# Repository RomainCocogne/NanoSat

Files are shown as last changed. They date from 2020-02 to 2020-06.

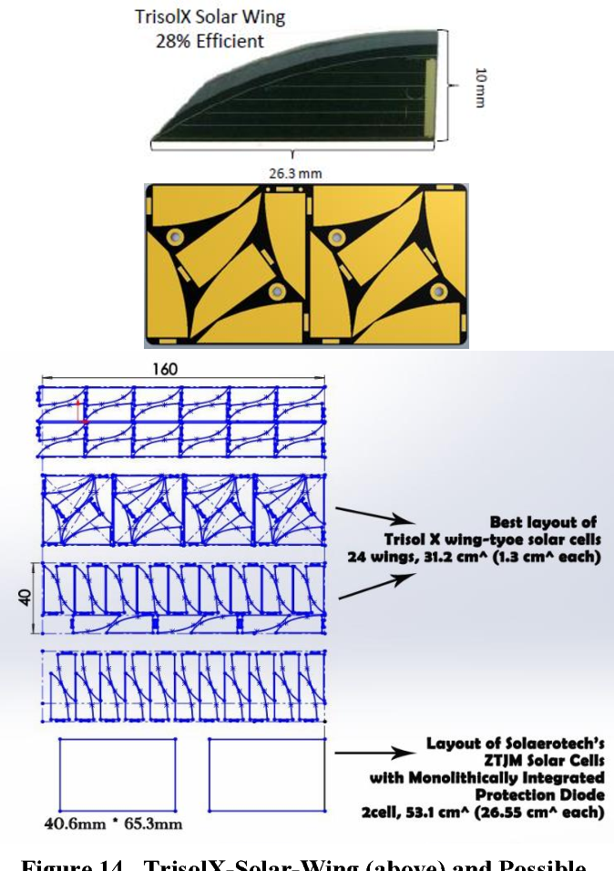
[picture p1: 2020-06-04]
datasheets/TRISOLX/trisolX_layout.png

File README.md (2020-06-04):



### Desciption
This repo is the current work of the Smart Solar Panel Project, an auxiliary project of NiceCube.
NiceCube is a NanoSatellite project.

You can find further informations on this project following this link



### Clone
If you want to clone this repo and continue the project, you need to be aware of some points

  - The code can be used as it is, but you should be carefull if you use another microcontroller. There may be some registers that need to be changed
  
  - The kicad projects use library included into this repo. If you open them as it is you might need to change the access path in kicad parameter tho.

### Contact
You can contact us using the following email adress

camille.brunin@univ-cotedazur.fr

quentin.combal@univ-cotedazur.fr

romain.cocogne@univ-cotedazur.fr

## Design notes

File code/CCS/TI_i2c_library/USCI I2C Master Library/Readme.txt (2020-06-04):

Using the USCI I2C Master

|--DMA Support : All files in this folder can be used ONLY ON MSP430 devices that have the USCI module AND DMA support.
    |------main.c : Application level C file that interfaces with slave MSP430 device. (Use TI_USCI_I2C_slave.c)
    |------TI_USCI_I2C_master_dma.c : Hardware interface level C file that contains all function definitions needed for USCI             initialization and USCI I2C communication.
    |------TI_USCI_I2C_master_dma.h : Header file that contains all definitions used in application/hardware interface files.

|--Without DMA Support : All files in this folder can be used on ANY MSP430 device with the USCI module
    |------main.c : Application level C file that interfaces with slave MSP430 device. (Use TI_USCI_I2C_slave.c)
    |------TI_USCI_I2C_master.c : Hardware interface level C file that contains all function definitions needed for USCI initialization      and USCI I2C communication.
    |------TI_USCI_I2C_master.h : Header file that contains all definitions used in application/hardware interface files.

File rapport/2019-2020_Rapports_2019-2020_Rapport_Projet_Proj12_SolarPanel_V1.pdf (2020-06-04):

1 | Polytech'Nice Sophia, Département électronique Les Templiers 930 Route des Colles - BP 145 06903 Sophia Antipolis Cedex

# Projets Industriels – Elec4

## Année scolaire 2019-2020

# Project Documentation

# Intelligent solar generator for Cubesat

## Version 1.0

Students : Brunin Camille, Combal Quentin,

# Cocogne Romain

# Tutors: Florentin Millour

# Company: Lab Lagrange

Département d partement d’ Electronique lectronique

2 | Polytech'Nice Sophia, Département électronique Les Templiers 930 Route des Colles - BP 145 06903 Sophia Antipolis Cedex

## THANKS

First of all, we would like to thank our project tutor, M. Florentin MILLOUR, for his time, patience and cheerfulness.

Thanks to M. Olivier PREIS too for having brought us to the observatory, it was a really rewarding experience.

Finally, thanks to M. JACOB and M. LANGELLA for their help and educational support.

3 | Polytech'Nice Sophia, Département électronique Les Templiers 930 Route des Colles - BP 145 06903 Sophia Antipolis Cedex

## TABLE OF CONTENT

4 | Polytech'Nice Sophia, Département électronique Les Templiers 930 Route des Colles - BP 145 06903 Sophia Antipolis Cedex

5 | Polytech'Nice Sophia, Département électronique Les Templiers 930 Route des Colles - BP 145 06903 Sophia Antipolis Cedex

# I.Introduction

NiceCube is a nanosatellite project that will allow the Lab Lagrange to do technological demonstrations by performing optical communications between earth and the satellite. NiceCube is a CubeSat type of satellite. It is relatively small, lightweight, and rectangle shaped. The challenges are to make NiceCube self-sufficient in terms of energy, and to gather data from its environment.

A satellite can be powered by different types of generators. The most common and easy-to-use type of generators are solar panels, because they take advantage of the satellite’s long exposure to sunlight in space. They can also be easily integrated in an electronic system. This is what we decide to use to power NiceCube.

Our mission is to conceive a smart solar panel that powers the whole satellite. It will be used as a solar generator and will be able to give us useful real-time information about the satellite. Indeed, we need to measure the current and voltage output of the solar panel, as well as its temperature, the relative location of the sun, and the earth horizon orientation. These measurements are needed to manage the solar cells and to determine the satellite’s orientation. Moreover, the solar cells will need to be electrically protected and individually deactivated if damaged.

In this document we will first go through the requirements of the project, then we will explain how we organized and compare what we planned to do and what we did. Finally, we will go over all the components and prototype’s specifications.

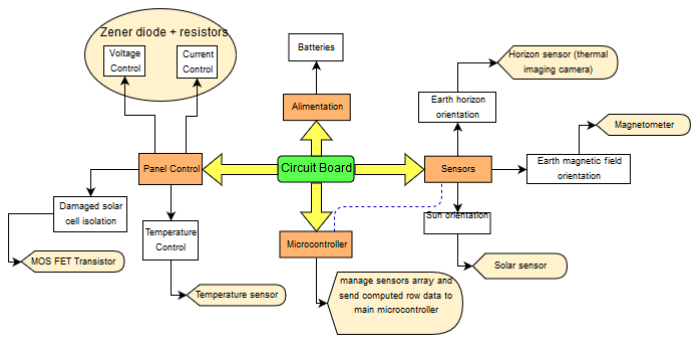
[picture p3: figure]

6 | Polytech'Nice Sophia, Département électronique Les Templiers 930 Route des Colles - BP 145 06903 Sophia Antipolis Cedex

# II.Architecture

## II.1.Block Diagram

Figure II.1 Architecture block diagram

The circuit board will be organized into four different parts described below.

## II.2.The solar panel

The first and core part of our project is the solar panel. The panel control is essential to make sure that the satellite is powered correctly. The panel is a “smart” panel, meaning it can manage itself.

The panel is made of several banks wired in parallel, with each bank made of multiple solar cells wired in series. The voltage output is determined by the number individual cells in each bank, and the current output is set by the number of banks on the panel.

Current and voltage measurements are performed to check if the cells are furnishing the required power for the whole satellite, or to detect a failure in the cell banks. We monitor the temperature of the cells as well with temperature sensors.
If one or several cell banks are damaged, they can be electrically disconnected from the circuit with MOSFET transistors. The command of these transistors is handled by the microcontroller.

## II.3.The main sensors

This is the part of the satellite that is used to gather data from the satellite’s environment. It includes three different types of sensors that are used to determine the current orientation of the satellite.

This part is composed of the following sensors:
- A solar sensor made of two 1-dimensional PSDs (Positional Sensitive Detectors) used to determine the position of the sun relative to the satellite
- A magnetic field sensor used to detect earth’s magnetic field and its relative direction
- A thermal imaging camera used to deduce earth’s horizon orientation from infrared radiation.

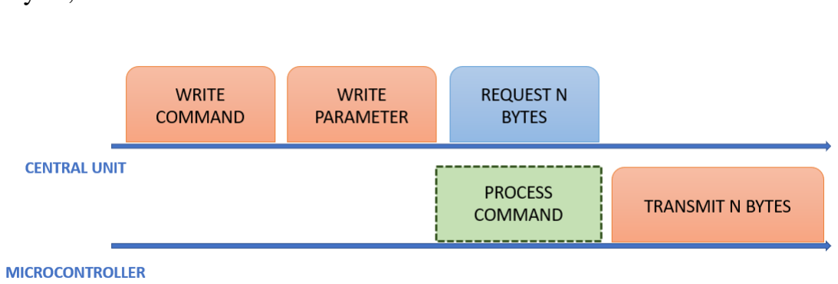
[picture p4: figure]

7 | Polytech'Nice Sophia, Département électronique Les Templiers 930 Route des Colles - BP 145 06903 Sophia Antipolis Cedex

These measurements are computed to deduce three vectors aligned with:
- The orientation of the sun
- Earth’s horizon
- Earth’s magnetic field

These vectors are then used by the satellite’s central unit to regulate its orientation.

## II.4.The microcontroller

The microcontroller’s duty is to manage the solar panel and the sensors. Its main tasks are:
- Managing the solar panel: checking the status of the solar banks through current and voltage measurements. Opening or closing the MOSFET transistors when a cell is damaged.
- Receiving commands from the central unit and sending back the required data
- Managing communication between the sensors

The sensors are accessed using an I²C bus in which the microcontroller acts as the master unit. Likewise, the communication with the central unit uses I²C in which the microcontroller is the slave.

The central unit sends a message containing an 8-bit command and an eventual 8-bit parameter. Upon receiving the command, the microcontroller executes it and holds the response in the buffer. The central unit then asks to receive the processed data, and the microcontroller starts transmitting. Data is transmitted in bytes, LSB first.

Figure II.2 Communication protocol between the microcontroller and the central unit

Below is a list of possible commands:

- READ_SENSOR: asks for a sensor's value. The sensor is specified with a parameter corresponding to a sensor’s id. There is also a specific parameter to ask for a measurement from every sensor.
- LIST_SENSOR: asks for a list of available and functioning sensors
- CONROLLER_STATUS: asks the controller to perform a self-status check and to report any malfunction, such as defective I/Os or unusual temperature.
- CELLS_STATUS: asks the controller to perform a status check on the solar cells.

## II.5.The power supply

This part would be the batteries, charged by our solar panel. However, we are not in charge of the batteries part. We just need to supply enough power to be able to charge them.

Our system needs to be self-sufficient, which mean we must design our system so it can be powered entirely by the solar generator.

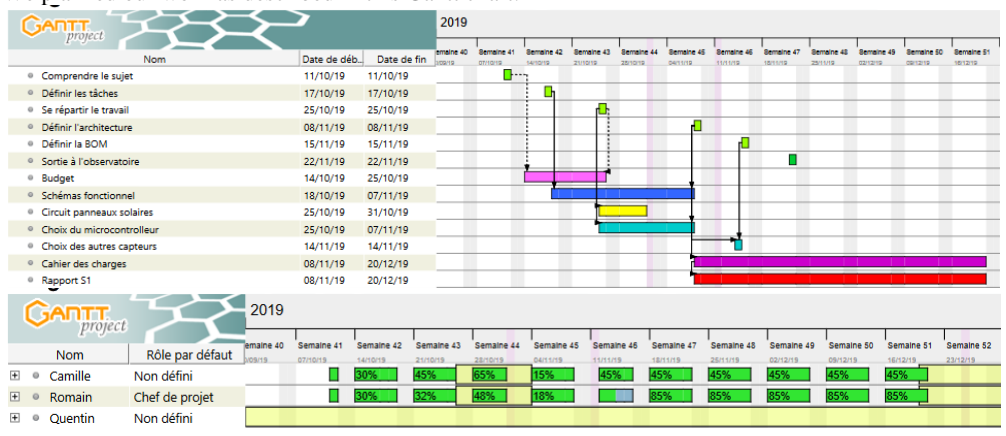
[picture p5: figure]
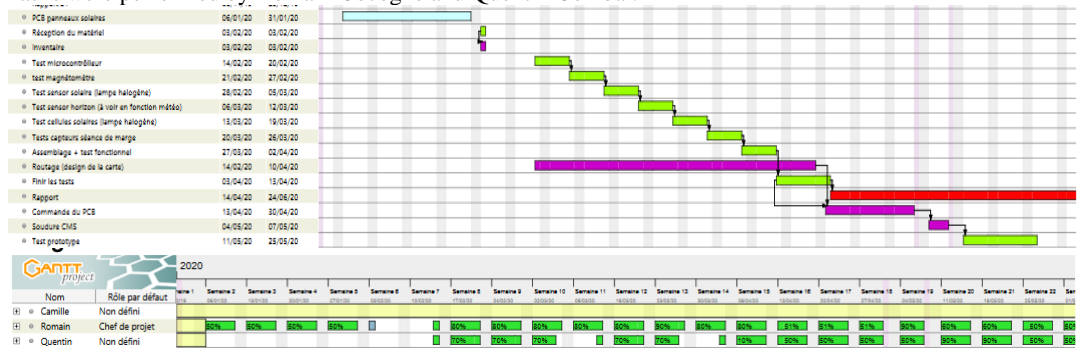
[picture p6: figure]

8 | Polytech'Nice Sophia, Département électronique Les Templiers 930 Route des Colles - BP 145 06903 Sophia Antipolis Cedex

# III.Plan and Tasks

## III.1.Objectives

The first semester was dedicated to defining the specifications of the project, describing a technical solution, and organizing the development. Tasks were performed by Camille Brunin and Romain Cocogne.

We planned our work as described in this Gantt chart.

Figure III.1 Semester 1 planned Gantt chart

During the second semester, we developed and adapted the solutions established during the first semester. Tasks were performed by Romain Cocogne and Quentin Combal.

Figure III.2 Semester 2 planned Gantt chart

## III.2.Reality

For the first semester, we managed to complete all planned tasks on schedule. We did re-shuffle the tasks because we were able to work on tasks in parallel, but overall the planning was accurate. You can see on the resources section that some of them were overloaded, but in reality, the workload was equally supported by both resources. This kind of temporary help can’t be transcribed into the Gantt software.

9 | Polytech'Nice Sophia, Département électronique Les Templiers 930 Route des Colles - BP 145 06903 Sophia Antipolis Cedex

Figure III.3 Semester 1 real Gantt chart

The second semester did not plan out as scheduled. Due to global lockdown caused by COVID-19 pandemic, we re-organized ourselves and changed our objectives, as described in the Adapting to the lockdown section. Overall, Quentin was responsible for most of the software development and Romain was responsible for the hardware development.
We also had one more prototype to do compared to what was planned in semester 1, so we had to squeeze some time for his development. We did have to remove some objectives such as working on the PSD to still be on schedule.

Figure III.4 Semester 2 real Gantt chart

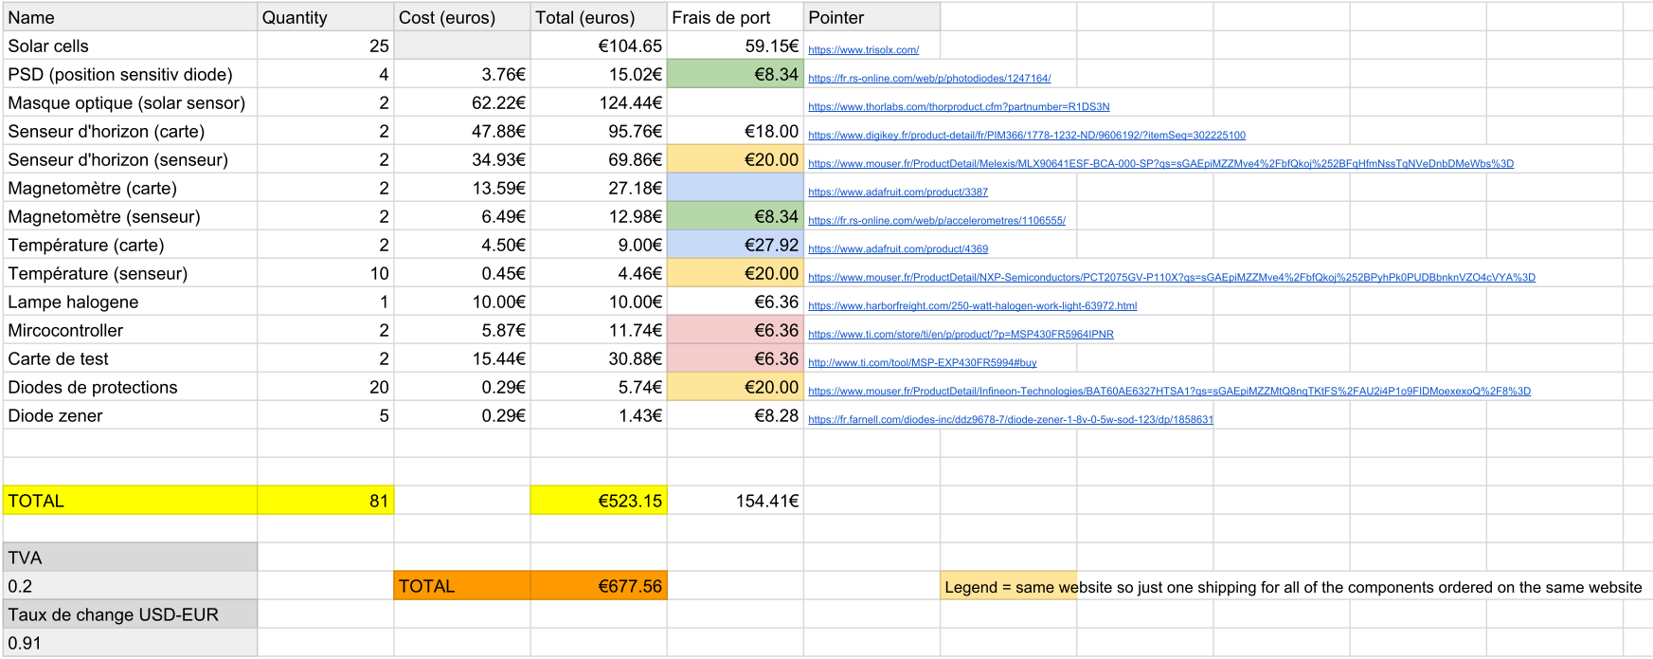
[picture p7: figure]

10 | Polytech'Nice Sophia, Département électronique Les Templiers 930 Route des Colles - BP 145 06903 Sophia Antipolis Cedex

# IV.BOM (Bill of material)

Figure IV.1 First BOM

We can see above the BOM computed from the data we had after one semester of work. After the second semester, all the main components remained the same, but we did add a lot of passives elements. We also added a current sensor, voltage reference and voltage regulator as described in the Development section. You can see below the BOM linked to the second prototype.

Figure IV.2 BOM of second prototype

Item | Qty | Reference(s) | Value | Datasheet
1 | 1 | AC1 | LSM9DS1TR | http://www.st.com/content/ccc/resource/technical/document/datasheet/1e/3f/2a/d6/25/eb/48/46/DM00103319.pdf/files/DM00103319.pdf/jcr:content/translations/en.DM0010331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
2 | 14 | C1, C5, C7, C23, C24, C25, C26, C28, C30, C31, C32, C33, C34, C37 | 100nF | ~
3 | 2 | C2, C3 | 1uF | ~
4 | 6 | C4, C8, C9, C10, C11, C29 | 10uF | ~
5 | 5 | C12, C13, C14, C15, C27 | 10nF | ~
6 | 1 | C22 | 2.2nF | ~
7 | 1 | C35 | 2.2uF | ~
8 | 1 | C36 | 47nF | ~
9 | 3 | D1, D2, D3 | D_Schottky | ~
10 | 1 | IC1 | MLX90641ESF-BAA-000-TU | https://www.mouser.com/datasheet/2/734/MLX90614-Datasheet-Melexis-953298.pdf
11 | 1 | IC2 | PCT2075DP,118 | http://www.nxp.com/docs/en/data-sheet/PCT2075.pdf
12 | 1 | IC3 | MSP430FR5964IPNR | http://www.ti.com/general/docs/suppproductinfo.tsp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
13 | 1 | J5 | HEADER_2x7_2.54MM
14 | 1 | J6 | 532610871 | ~
15 | 14 | Q1, Q2, Q3, Q4, Q5, Q6, Q7, Q8, Q9, Q10, Q11, Q12, Q13, Q14 | RUR040N02HZGTL | ~
16 | 7 | R1, R4, R7, R10, R14, R29, R31 | 20R | ~
17 | 7 | R2, R5, R8, R11, R15, R30, R32 | 1M | ~
18 | 3 | R3, R6, R9 | 100mR
19 | 13 | R12, R13, R16, R17, R18, R27, R28, R39, R40, R41, R42, R43, R44 | 330R
20 | 1 | R19 | 47kR
21 | 11 | R20, R21, R22, R23, R24, R25, R26, R33, R34, R35, R36 | 10k
22 | 1 | R37 | 3.3k
23 | 1 | R38 | 2k
24 | 12 | SC1, SC2, SC3, SC4, SC5, SC6, SC7, SC8, SC9, SC10, SC11, SC12 | Solar_Cell | ~
25 | 1 | SW1 | BP_DROIT_TRAV-switch
26 | 1 | U1 | LT1790ACS6-1.25TRMPBF | LT1790ACS6-1.25#TRMPBF
27 | 2 | U2, U3 | S3274-05
28 | 1 | U4 | NCP59302DSADJR4G | http://ww1.microchip.com/downloads/en/DeviceDoc/MCP14A0303_4_5-Data-Sheet-20006046A.pdf
29 | 1 | U5 | INA3221AIRGVR | Texas Instruments

11 | Polytech'Nice Sophia, Département électronique Les Templiers 930 Route des Colles - BP 145 06903 Sophia Antipolis Cedex

# V.Estimated budget

During the first semester, we were able to estimate the budget by taking into account all of the factors as if we really started this project from scratch. First, we estimated our salaries as engineers and our tutor’s salary. It gave us a total of 6 007€.

Figure V.1 Estimated salaries

Then, we estimated the travel costs for us and our project tutor, which led us to a total of 1 299.96€.

Figure V.2 Estimated travel costs

After that, we had to calculate the costs of the material that we are going to buy and rent, for a total of 2207.56+117 = 2324.56€.

12 | Polytech'Nice Sophia, Département électronique Les Templiers 930 Route des Colles - BP 145 06903 Sophia Antipolis Cedex

Figure V.3 Estimated cost of material

Figure V.4 Estimated cost of renting equipment

Finally, we arrived at a total of:

13 | Polytech'Nice Sophia, Département électronique Les Templiers 930 Route des Colles - BP 145 06903 Sophia Antipolis Cedex

# VI. Components specifications

## VI.1.MICROCONTROLLER

The microcontroller needs to manage the sensor network, control the well-being of the solar cells, and communicate with the satellite’s central unit. It needs to embed at least two hardware I²C modules, so that it can manage one I²C bus for sensor communication, and another bus to exchange data with the central unit. It must have at least 6 analog pins for current and voltage measurements. Most importantly, the microcontroller needs to be optimized for ultra-low power consumption.

Following the advice of our tutor Florentin Millour, we looked towards the MSP430 microcontrollers (https://www.ti.com/lit/ug/slau367p/slau367p.pdf?ts=1590224617008) from Texas Instruments. This family of microcontrollers is known for its low power capabilities and is widely used in similar projects where reducing consumption is essential.
The MSP430FR59XX (https://www.ti.com/lit/ds/symlink/msp430fr5949.pdf?ts=1590224343299) microcomputer family has the following characteristics:
- Up to 256KB of Ferroelectric Random Access Memory (FRAM) with ultra-low power writes
- Optimized Ultra-Low-Power Modes, 350 nA consumption when on standby with a Real Time Clock
- Multifunction I/O ports, 40 to 68 depending on the model
- Up to 4 hardware I2C modules

The MSP430FR59XX (https://www.ti.com/lit/ds/symlink/msp430fr5949.pdf?ts=1590224343299) satisfies all of the aforementioned requirements.

## VI.2.SENSORS

VI.2.1.Solar sensor
We need to sense the satellite’s orientation compared to the sun. Knowing the required angle precision between the satellite and the antenna is 10°, the sensor needs a 3° precision in the worst case. The technology used is a masked one-dimensional PSD (depth of the mask is 1.5mm), so the corresponding length precision of the diode is 78um maximum.
The S3274-05 model gets a 35um maximum precision, which is under the specification. This PSD needs an under 300um wide light ray. The R1DS3N mask has a 10um wide strip line.

VI.2.2.Magnetometer
We need to measure the satellite’s inclination compared to the earth’s surface. We will use a magnetometer to sense the earth’s magnetic field.
As the solar sensor, we need a 3° precision in the worst case.
Knowing the earth’s magnetic field of 05Gauss, we found a maximum error of 26mGauss.
The LSM9DS1’s precision is 0.14mGauss for 4Gauss magnetic fields and under. This corresponds to a 0.02° error. We are well under the specifications.

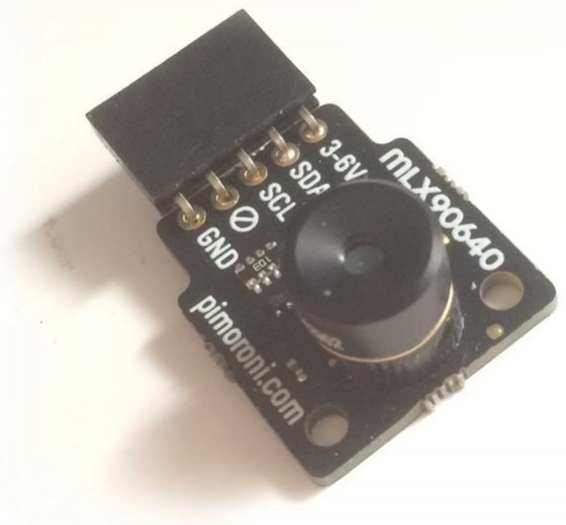
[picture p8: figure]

14 | Polytech'Nice Sophia, Département électronique Les Templiers 930 Route des Colles - BP 145 06903 Sophia Antipolis Cedex

Figure VI.1 LSM9DS1 magnetic sensor on a prototyping board from Adafruit.

VI.2.3.Horizon sensor
We need another vector to angle the satellite compared to the earth, so we need to use a horizon sensor. Just like the other sensor, this one needs a 3° precision in the worst case.
The MLX90641 is a 16x12 pixel thermal camera with a field of view of 110°, giving us a 9°/pixel precision. It means we have a 2.6° precision in the camera. Although we can use this camera, further tests need to be done to see if we are not under the 3° error. If that’s the case, a more power costly camera could be considered. The MLX90640, for example, has a resolution of 32x24 pixels.

Figure VI.2 MLX90640 32x24 thermal camera

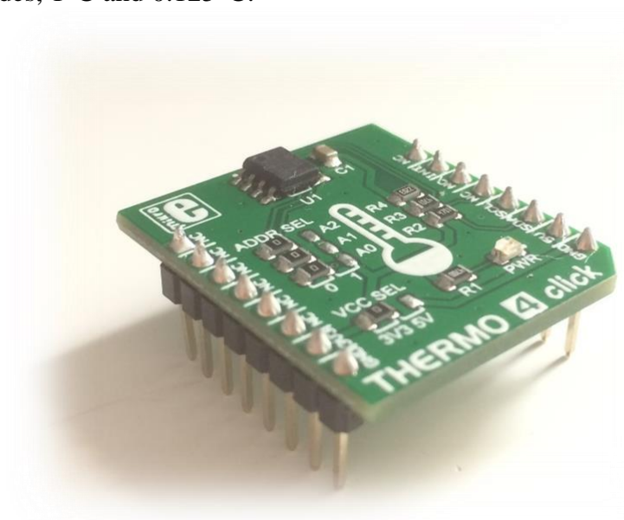
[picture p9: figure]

15 | Polytech'Nice Sophia, Département électronique Les Templiers 930 Route des Colles - BP 145 06903 Sophia Antipolis Cedex

VI.2.4.Temperature sensor
This sensor is needed to control the panel’s temperature. We can put a sensor in the center of the panel and another sensor opposite to the microcontroller to check if there is no overheating. There is no need for a big precision, as we want to measure big temperature variation. A 1°C precision is enough for us. The LM75A has two resolution modes, 1°C and 0.125°C.

Figure VI.3 LM75A temperature sensor on a prototyping board from Mikroe Electronika

VI.2.5.Voltmeter
We need to measure the volt variation (drops and peaks) to check the state of our solar cells. We will use the analog pin of our micro-controller, with a max voltage input of 3.3V. To get maximum precision over the measurement, we take the voltage reference at 1.15V.
To make a voltage reference, we need to use a Zener Diode. As there is no Diode with a Zener voltage under 1.8V, we take 1.8V as a reference. With this, we can detect a voltage drop under 2V, which is enough to detect one solar cell’s failure.

VI.2.6.Amperemeter
To complement the voltage measurement, we need a current variation measurement. We will use resistors in series with the solar cells and measure the resulting voltage. As the solar cells current is around 14mA, the analog pin of our microcontroller will be enough to detect a current drop.

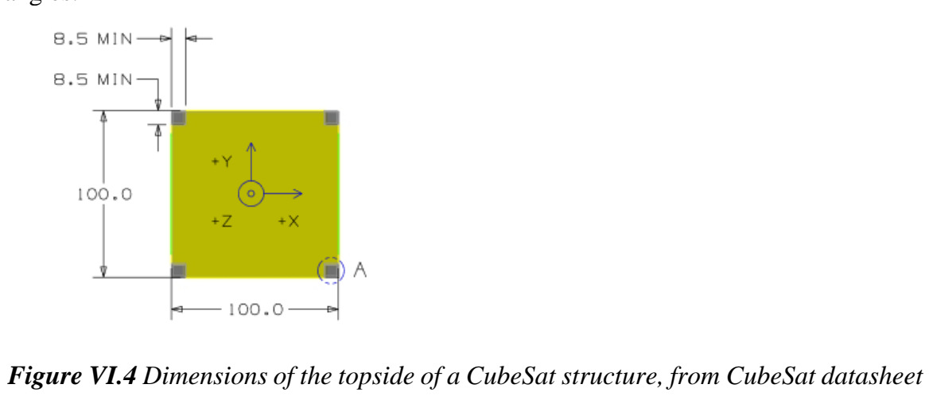
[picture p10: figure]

16 | Polytech'Nice Sophia, Département électronique Les Templiers 930 Route des Colles - BP 145 06903 Sophia Antipolis Cedex

## VI.3.SOLAR CELLS

The system needs to be compatible with the CubeSat structure, meaning a 10x10cm² surface with truncated angles.

The yellow plane above is the available space for our system.
Following the advice of our tutor, we use TrisolX solar cells. TrisolX cells are relatively cheap and are optimized for space applications. They are often used for similar projects.

Each one is approximately 2.6cm². We use a 5mm margin around each cell. Considering the cells will be using 60% of the total panel surface, we can place a total of 12 cells onto our panel.
After testing, the ratio will be adjusted and more panels will be added, but for the prototypes, this ratio will be enough.

The batteries’ control system is GOMSpace, nanopower p31u. (https://gomspace.com/UserFiles/Subsystems/datasheet/gs-ds-nanopower-p31u-27.pdf) As stated in the datasheet, we need to deliver between 4.2V and 8.5V. Knowing the cells are 2.33V max each, we will put 4 cells in series to deliver the correct voltage. As we can use 12 cells, we will make a 4x3 cell matrix.

To protect each line, we put a Schottky diode in series with the 4 cells.
Here is a schematic of one solar bank configuration taken from Prototype 1 schematic.

Figure VI.5 Solar bank schematic

Figure VI.4 Dimensions of the topside of a CubeSat structure, from CubeSat datasheet

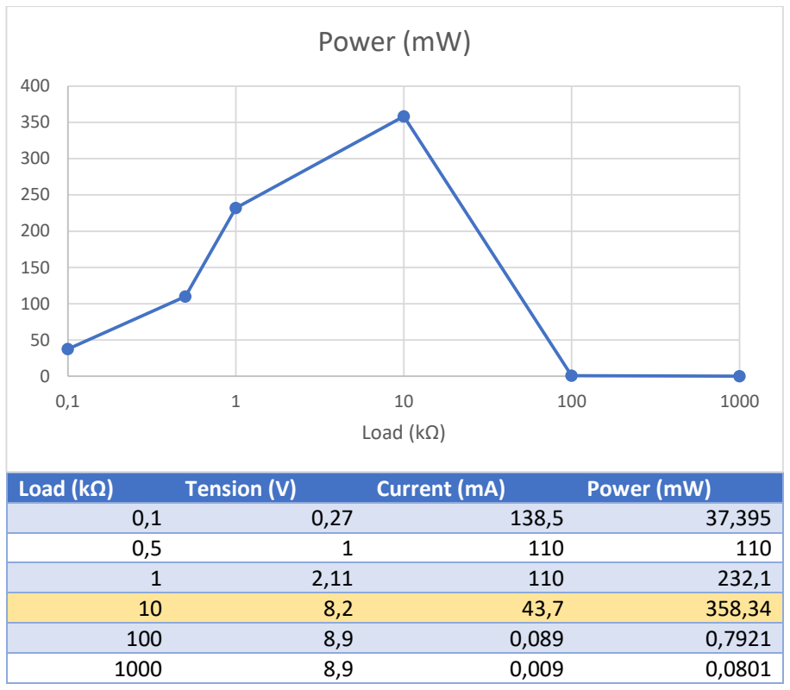
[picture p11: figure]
Load (kΩ); Tension (V); Current (mA); Power (mW)

17 | Polytech'Nice Sophia, Département électronique Les Templiers 930 Route des Colles - BP 145 06903 Sophia Antipolis Cedex

# VII.Development

## VII.1.Solar cells

VII.1.1.Power characteristics
We need to know the best load to put on the solar bank to maximize the power output. To do that, we try different load and measure voltage and current output. In our testing setup, we used a 400W halogen lamp. Halogen lamps provide a luminous spectrum very similar to the sunlight spectrum, and we want to get as close as possible to that spectrum to get realistic tests. The lamp was placed at 10cm from the solar cell testing board. We computed the results into the following curve.

Figure VII.1 Power generation of one solar cell relatively to circuit load.

We can see the optimum load of 10k can provide us with 350mW of power.

VII.1.2.Voltage Reference
At first, we tried to use a Zener diode to provide constant output voltage, but as explained in Prototype 1 category, the result was not satisfactory. We chose to add a dedicated circuit.
We took the MCP1501. It provides a constant 1.25V as reference, with 0.08% of precision. It is possible to shut down the device using the SHDN pin, so we can reduce power consumption.

VII.1.3.Voltage regulator
To power all sensors and the microcontroller, we needed to add a 3.3V voltage regulator. We took the NCP59302DSADJR4G adjustable voltage regulator for his low dropout voltage, its wide output current range and its supply voltage working range (still working with 1.2V input).

18 | Polytech'Nice Sophia, Département électronique Les Templiers 930 Route des Colles - BP 145 06903 Sophia Antipolis Cedex

VII.1.4.Amperemeter
To measure each solar bank’s current input, we first used a shut 20Ω resistor. As explained in Prototype 2, this method doesn’t provide a stable enough output, so we added a dedicated circuit instead.
We chose the INA3221 triple-channel current and voltage monitor because of his I2C compatibility, the ability to monitor 3 solar banks at the same time and his programable alert and warning outputs, allowing us to deport current monitoring to the sensor.
The shut resistors are in turn way smaller, consuming less power from the solar panels.

Figure VII.2. INA3221 TI current and voltage monitor

## VII.2.Microcontroller and sensors interfacing

We were unable to get a micro controller from the MSP430FR59XX family. Instead, we used a MSP430G2553 from Texas Instrument, which provides similar features regarding ultra-low power modes but offers less I/O ports and only one hardware I²C module.

All the sensors we are using communicate their data through I2C busses. The MSP430G2553 has one built-in I2C hardware module that we can use. To develop, calibrate, and prototype our system, we used the MSP430 LaunchPad from Texas Instruments. The LaunchPad is a development board that allows us to easily program our MSP430G2553 microcontroller using a USB connection.

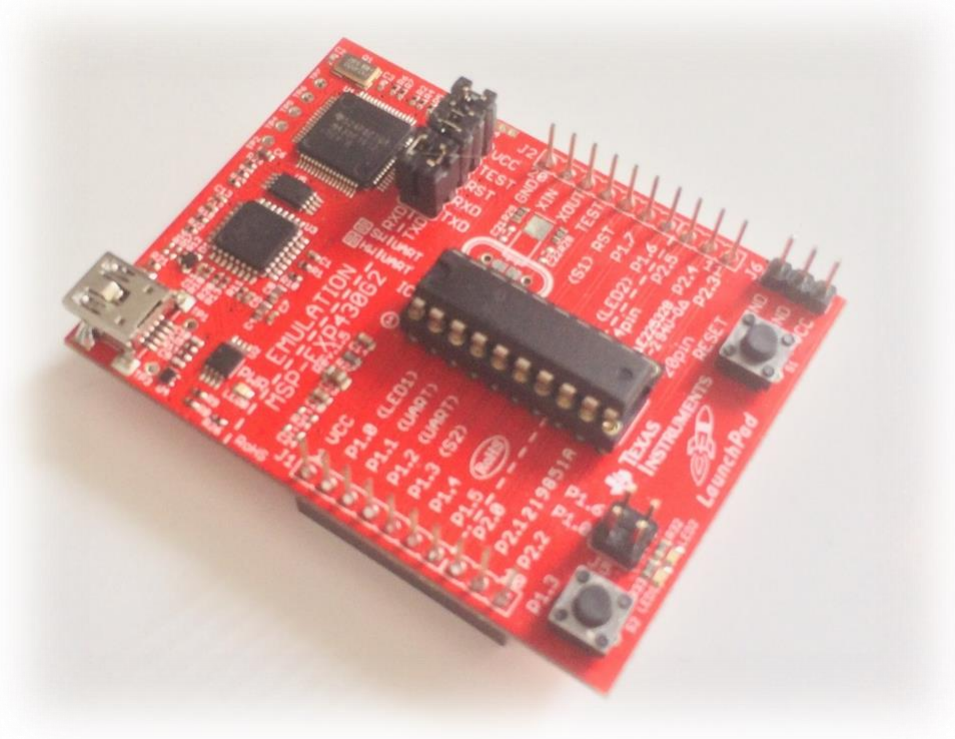
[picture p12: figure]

19 | Polytech'Nice Sophia, Département électronique Les Templiers 930 Route des Colles - BP 145 06903 Sophia Antipolis Cedex

Figure VII.3. MSP430 Launchpad with an MSP430G2553 microcontroller

VII.2.1.Code development
To program the MSP430G2553 and use its hardware modules we used the Energia IDE. Energia is a modified version of the Arduino IDE that comes with custom libraries for specific use with development boards from Texas Instruments, such as our MSP430 Launchpad. This is useful for prototyping because we have access to the standard Arduino libraries that we are used to using. The program is written in a simplified C++ language, identical to the Arduino syntax.
To establish the I2C communication we use the Wire library from the standard Arduino libraries. We developed one code per sensor for independent testing and calibration.
We also need to use the ultra-low power capabilities of the MSP430G2553. This requires a lower level of access than what Energia provides us. We used the Code Composer Studio (CCS) IDE developed by Texas Instruments for their LaunchPad. With CCS we program the microcontroller at Register-Transfer Level using C code. Moreover, this IDE provides useful power optimization advice upon compilation. We can also import code made with Energia into CCS. With this environment, we can first develop a prototype using a higher-level language, and then modify it at a lower level for fine-tuning.

The Wire library was useful for the first functional tests of the sensors, but it is relatively slow, and the library is code heavy. We decided to use the USCI_I2C_master library from TI application examples. It is a light I2C library written in C, we had to tweak it to make it work with our specific model of microcontroller.

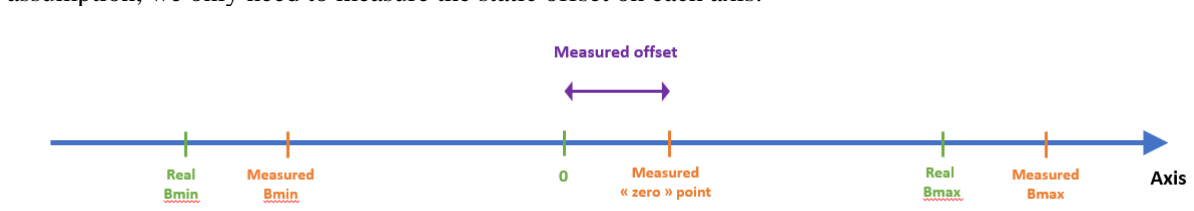
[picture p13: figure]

20 | Polytech'Nice Sophia, Département électronique Les Templiers 930 Route des Colles - BP 145 06903 Sophia Antipolis Cedex

## VII.3.Sensor calibration

Each of our sensor might suffer from a bias, or a distortion, in the measurements. This can happen due to an imprecision during the manufacturing, or a physical phenomenon. This bias is generally small, but we need to take it into account nonetheless, which means we need to be able to measure it. In this section we explain the protocols used to calibrate our sensors.

VII.3.1.LM75A – Temperature sensor
To calibrate the LM75A, we need to measure the temperature of an object whose temperature is known to us. We can then compare the theoretical value to the measured value. The easiest example of such an object is water that is changing phase. We know that the temperature of water stays constant during the transition between two states. We also know the temperatures at which water changes phases. So, if we measure the temperature of water during a phase transition, we should get a consistent result. We decide to measure the temperature of ice cubes that are melting.
We assume the atmospheric pressure during the measurements is equal to 1 bar, which means the temperature of water is 0°C when melting.

Measured temperature of the ice-water mixture: 0.25°C with 0.125°C precision
We determined that our LM75A sensor has a static offset of +0.25°C

VII.3.2.LSM9DS1 – Magnetometer
The magnetometer measures the intensity of the magnetic field along 3 directional axes. We can assume that the axes are aligned as they should be, meaning that they form an orthogonal 3D base. With that assumption, we only need to measure the static offset on each axis.

Figure VII.4 Magnetometer offset schematic

To measure the offset on one axis, a simple test consists of finding the minimum and maximum values on the axis. The offset is the mean value of those extrema. In order to calibrate the LSM9DS1, we need to measure the extrema values on each axis.

The code used to calibrate the sensor can be found in the Annex section. It performs continuous measurements of the magnetic field on each axis and displays the maximum and minimum values on each axis so far. It also displays the resulting offset of those measurements. While this code runs, we rotate the sensor in every direction until the offset readings are stable.

We got the following values:
X offset: +122.5 mGauss
Y offset: +143.36 mGauss
Z offset: +56.35 mGauss

21 | Polytech'Nice Sophia, Département électronique Les Templiers 930 Route des Colles - BP 145 06903 Sophia Antipolis Cedex

VII.3.3.AMG88xx Thermal Camera
Due to time constrain, we only managed to make a working test code with the AMG8833 camera, an 8x8 pixels thermal camera with an Adafruit library. We managed to test the horizon’s detection algorithm with this camera.

Figure VII.3 AMG8833 thermal camera

We need to extrapolate the position of the satellite with the output of the camera, which is an 8x8 pixel array. To get the horizon, we made a linear regression using the matrix formula
(INDEXT
∗ INDEX)

−1

∗ INDEXT
∗ V | (VII.3.3.1)
with V = (

x1
x2
⋮

) , the matrix filled with the pixel position of detected horizon, and INDEX = (

1 1
2 1

⋮ ⋮ ) with

the same length of V.
We get the matrix C = (

a
b

), with a, b the coefficients of the linear expression of the horizon

y = a ∗ x + b | (VII.3.3.2)
We then need to calculate corresponding angles of the satellite position compared to the horizon. We choose the angles α and β as described in the following schematic.

Figure VII.4 Relation between horizon and angles

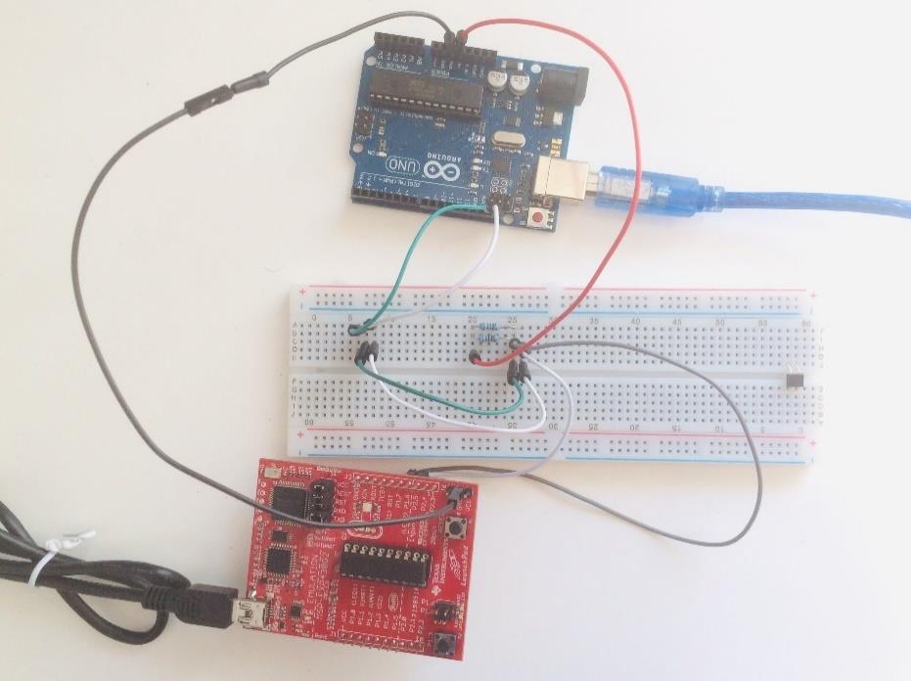
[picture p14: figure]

22 | Polytech'Nice Sophia, Département électronique Les Templiers 930 Route des Colles - BP 145 06903 Sophia Antipolis Cedex

From our linear expression, we can deduce α and β with the following formula in the XY plane (3.5 corresponds to the center of the screen).
αxy = tan⁻¹

(

−1
a
) | (VII.3.3.3)

βxy =

π
6

∗

1
3.5

∗

|3.5(1−a)−b| √a 2+1 | (VII.3.3.4)

And in the YX plane.

αyx =

π
2

− tan⁻¹

(

−1
a
) | (VII.3.3.5)

βyx =

π
6

∗

1
3.5

∗

|3.5(1−a)−b| √a²+1 | (VII.3.3.6)

We did the operation in both planes as, depending of the orientation of the satellite, one projection can be more precise than the other (we have more points in the matrix). We then need to compute the average value.
α =
αyx∗nbpointsyx+αxy∗nbpointsxy nbpointsyx+nbpointsxy | (VII.3.3.7)

β =

βyx∗nbpointsyx+βxy∗nbpointsxy nbpointsyx+nbpointsxy | (VII.3.3.8)

As you can see, we need to guard against limits values, such as a=0. We can explicitly calculate those values when we do the code implementation.
You can see the translation of these equations to an Arduino test code in the Annexes, Code, Thermal Camera section.

## VII.4. Communication with central unit

VII.4.1. Hardware setup
We do not have a lot of specifics about the central unit. But we know that it requires the values read on the sensors and communicates with the microcontroller on an I2C bus. To develop that communication, we used an Arduino Uno R3 board with an ATMEGA328p controller to act as the central unit. We used 10kΩ pull-up resistors on the I2C lines.

Figure VII.5 I2C communication between an MSP430 launchpad and an Arduino Uno R3.

23 | Polytech'Nice Sophia, Département électronique Les Templiers 930 Route des Colles - BP 145 06903 Sophia Antipolis Cedex

Because we are using the MSP430G2553 model instead of the MSP430FR59XX, we only have access to one hardware I2C. Therefore, we can’t test the sensor network and the communication channel with the central unit at the same time, as they require separate I2C buses. We considered using a virtual I2C interface to solve this problem, but we could not find any library for that purpose in C for MSP430 microcontrollers. Moreover, trying to develop our own virtual I2C library would have been time-consuming. We decided to test the communication protocol and the sensor network separately.

VII.4.2.Software setup
The central unit acts as the master on that I2C bus, and the MPS430 microcontroller acts as a slave. The master sends a command to indicate, for example, that it needs a value from the sensors. The microcontroller receives the command, reads one or multiple values from the sensors, processes the values if needed (ex: linear regression to detect the earth horizon as shown in VIII.3.3), and sends the result back to the central unit.

To make the MSP430G2253 act as a slave in the I2C communication we based our program on the TI_USCI_I2C_slave firmware example from Texas Instruments and modified it to make it compatible with our specific model of microcontroller. This small library is written in C and is very light (~100 lines of code). To make the Arduino act as a master we used the Wire library. We wrote a demo program in which the master tests all the available commands.

## VII.5.Prototypes

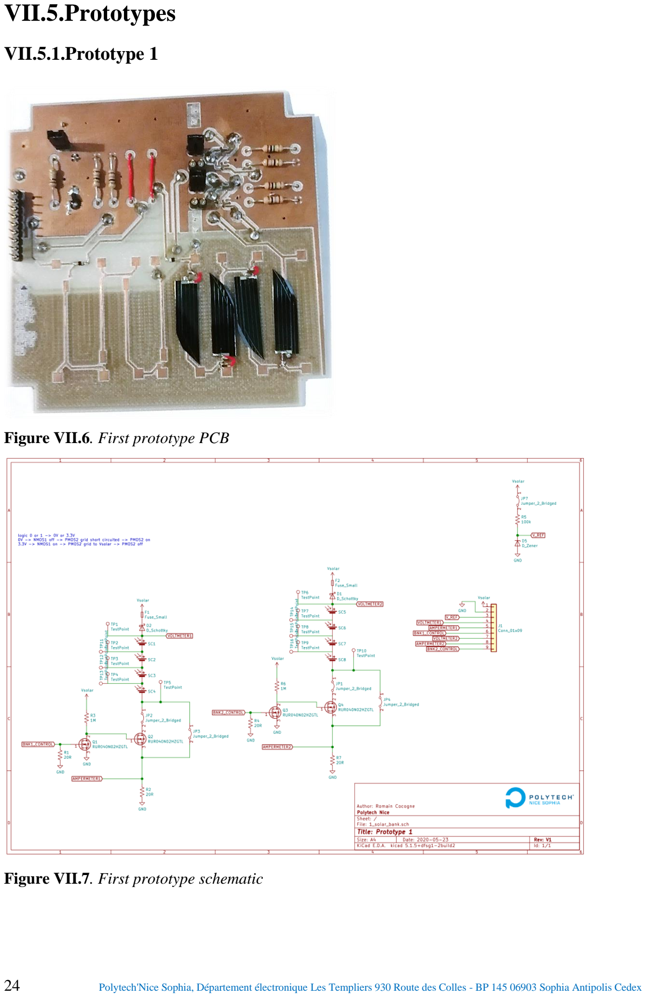
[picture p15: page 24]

24 | Polytech'Nice Sophia, Département électronique Les Templiers 930 Route des Colles - BP 145 06903 Sophia Antipolis Cedex

VII.5.1.Prototype 1

Figure VII.6. First prototype PCB

Figure VII.7. First prototype schematic

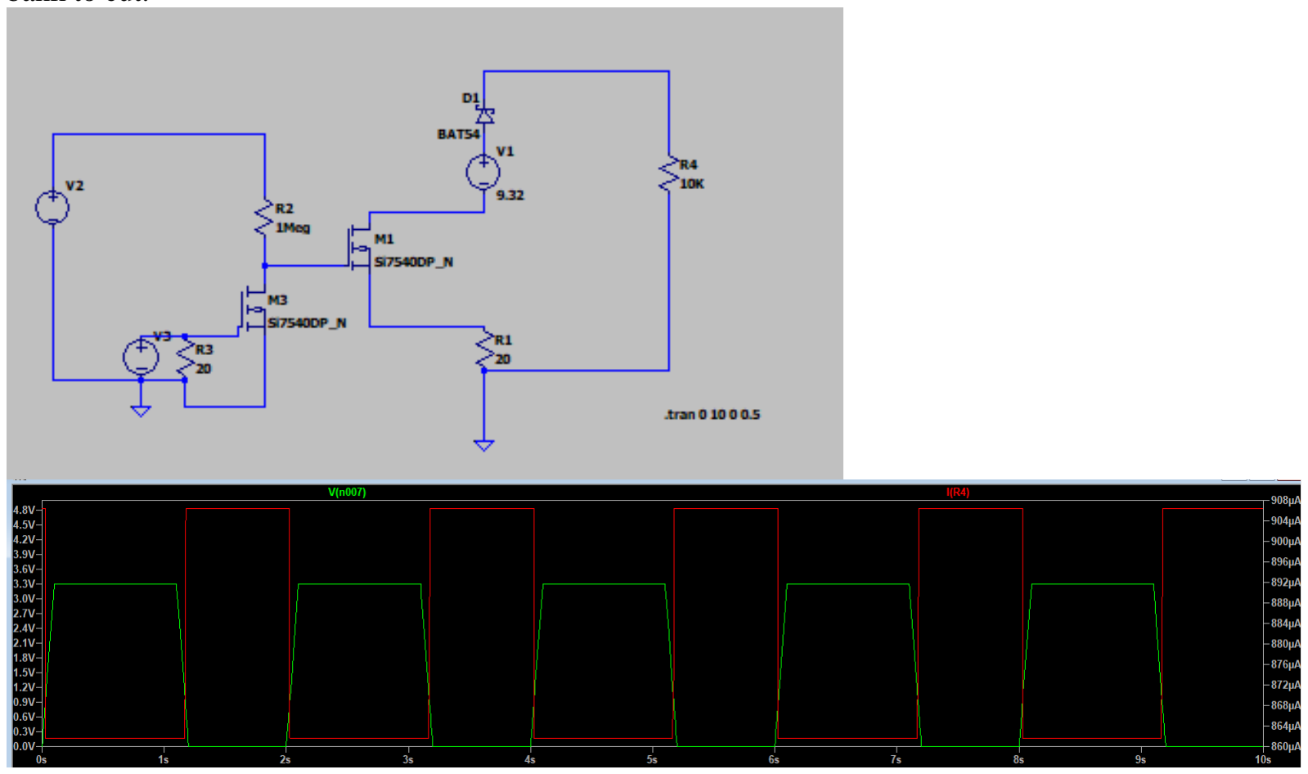
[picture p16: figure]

25 | Polytech'Nice Sophia, Département électronique Les Templiers 930 Route des Colles - BP 145 06903 Sophia Antipolis Cedex

The first prototype aims at testing only some functionalities of the solar panel.
We want to use this prototype to establish f(I) = V of one solar bank, check if the cut-of circuit of the bank works and if Vref is stable enough.
This prototype highlighted that the polarity of our cells was inverted, so the voltage output was negative. The voltage reference was not stable enough with wide variation of input voltage, with around 30% of deviation. We revised the schematic in Prototype 2 to integrate a dedicated reference circuit, explained in the Voltage Reference part.
The footprint of the solar cells was not well adapted and caused some cells to break, so we revised the footprint as seen in the layout of prototype 2.
We tested the amperemeter function and the result was not to our satisfaction. The resistor output was not stable enough to extrapolate running current. We needed a dedicated circuit to measure current with precision. We revised the schematic in Prototype 2 to integrate a dedicated amperemeter circuit, explained in the Amperemeter part.

This prototype was useful to compute the power characteristics curve and find the optimum load to put on the solar panels.
We didn’t manage to test the cut-of circuit because of delays in components delivery. Before printing the second prototype PCB, it is advised to test this feature. We nonetheless did a Spice simulation and the result was to our satisfaction. You can see below the result with V3 in input (green trace) and IR4 in output (red trace). The circuit lets the current flow through the load if the input is a logic ‘0’ and cut the current if the input is a logic ‘1’. This configuration allows the microcontroller to boot up before choosing which solar bank to cut.

Figure VII.8. Simulation of cut-of circuit

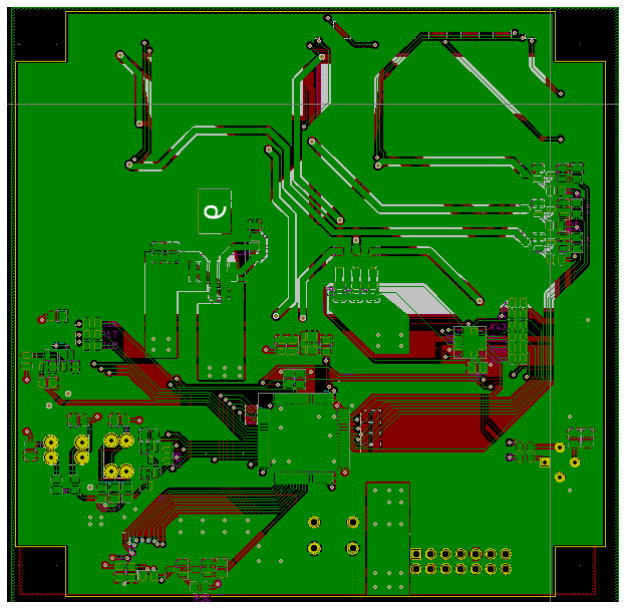
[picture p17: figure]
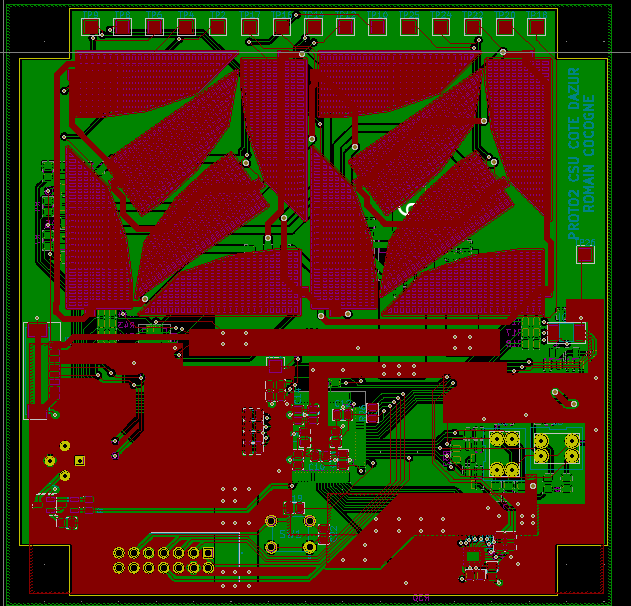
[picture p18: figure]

26 | Polytech'Nice Sophia, Département électronique Les Templiers 930 Route des Colles - BP 145 06903 Sophia Antipolis Cedex

VII.5.2.Prototype 2
For this prototype, we implemented all changes pointed out in prototype 1. You can study the schematics following this link to the Annexes, Schematics part.
We wanted to test the I2C bus and the working of our sensors. This prototype can also be used to test the code integration and the main software.
Due to time constrains, we didn’t print the PCB, but we finished the layout. All the passives components are in 0805 dimensions to ease the soldering further prototypes can use smaller packages to gain space. We have a 2 layers board to reduce production cost, but in fine it should be best to go with a 6 layers board with internal layers as ground or power plane. This will keep all sensitive components protected from space hazards.
We added one more solar bank to test the cube layout you can see below. This should be an optimized layout according to FigureVII.11.

Figure VII.11. Second prototype layout

Figure VII.9. TrisolX layout comparison

27 | Polytech'Nice Sophia, Département électronique Les Templiers 930 Route des Colles - BP 145 06903 Sophia Antipolis Cedex

The prototype is delivering the solar bank voltage as well as the I2C bus pins. This bus can’t be used to test I2C communication with the CubeSat’s main microcontroller. Its only use is to monitor the communication between our microcontroller and the sensors array.
The microcontroller is programmable through a JTAG connection.
To measure all the different voltages on this board, you can use the tests pads marked on the front face.

Here are some improvements and new features to add in the next prototype.
- Implement an EEPROM next to the microcontroller to keep permanent logs of sensors and panels state
- Add LED indicators to check if the board is powered up
- Add access pin to the microcontroller
- Add a second I2C bus output to try communicating with the main microcontroller

28 | Polytech'Nice Sophia, Département électronique Les Templiers 930 Route des Colles - BP 145 06903 Sophia Antipolis Cedex

# VIII.Challenges

## VIII.1. Technological challenges

One of the challenges that we faced was that we needed to learn how to use the MSP430 microcontroller and its embedded hardware modules. Setting up an efficient programming environment for prototyping took longer than we expected. The Launchpad development board does not benefit from a large community support, unlike Arduino boards for example. We could not always find existing libraries to answer our needs, which led us to rewrite libraries using register transfer operations. This made the development take more time than what we originally expected.

The routing of the second prototype was also a big challenge. Indeed, the board is inside a 100cm² square and a lot of components needs to fit in there. The 2 layers constrain did add a lot of complexity because some tracks were intertwining and crossing each other most of the time. Changing the orientation and disposition of the sensors helped resolve most of the problems, but sometimes we had no other choice but to modify the microcontroller pinout.

## VIII.2. Adapting to the lockdown

The global lockdown that started on March 16th in France in reaction to the COVID-19 pandemic was a major slowdown in the development of our project, due to its hardware nature. We had to reconsider our objectives and our organization.

We split the components so that we could work on separate parts and continue the development. Romain kept the solar cells, the halogen lamp, the first prototype, and soldering materials to be able to perform more tests and develop the schematic and routing for the second prototype. Quentin kept the microcontroller development board, the thermometer, and the magnetic sensor to develop the sensor interfacing and the I2C communication. Regarding the thermal cameras, we both kept one model, the 8x8 AMG88 for Romain and the 32x24 MLX90640 for Quentin. We also both kept one photo diode to try to develop the solar sensor. Fortunately, we had some electronic components at our homes, as well as Arduino boards that were very useful for prototyping.

To keep in touch with our tutor Florentin Millour, we organized weekly group calls using Skype and Zoom. It was essential to keep Mr. Millour informed on the advancements of the project, and to get his advice on where to put our focus in the development.

We tried to issue a new RS order, but due to unforeseen delays caused by current circumstances, we were not able to receive the components in time. Our tutor did provide us with some of his personal hardware such as his own MSP430 development board but there was some mismatch between the microcontrollers model and some features were not tested.

We ultimately had to lower our objectives. As we did not have access to the electronic lab anymore, we were unable to produce our second prototype. Instead we decided to focus on making the core parts of the project functional.

29 | Polytech'Nice Sophia, Département électronique Les Templiers 930 Route des Colles - BP 145 06903 Sophia Antipolis Cedex

# IX.Current state of the project

The core parts of our project, like the schematic for the solar cells or the I2C communication, are working as intended. The next step in the project would be to produce a prototype that links those core parts to test their interactions. We could not achieve all the objectives that we had planned. However, we provided a baseline of the different parts so that the project can be continued in the future.

In the following sections we summarize which parts of the project we consider functional, and which parts require further work.

## IX.1.Parts that are functional

IX.1.1.Solar cells electronic schematic
We designed an electronic schematic to manage the solar cells. The solar panel groups the solar cells into banks that deliver an 8.2V output with a max current of 43,7mA per bank. Individual banks can be disconnected by toggling an input on MOSFET transistors.
Simulations of this electronic system were performed on LTSpice and were successful. However, we could not perform practical tests as we could not access the equipment to produce a prototype. Further testing would be needed to ensure that the system works as intended with the microcontroller ports.

IX.1.2.Thermometer, magnetic sensor
We wrote functional programs in C for both the thermometer and the magnetic sensor. The program files are light and use direct register access on the hardware I2C module, making the execution relatively fast. As of now, each sensor has its own program in separate CCS project directories, but the two programs can be easily combined assuming the sensors are on the same I2C bus. The library used to exploit the I2C module can be used as a baseline to write programs for the other sensors.

IX.1.3. 8x8 thermal camera
We performed tests on the AMG8833 8x8 thermal camera and implemented the algorithm described in Sensor calibration Section. Those first tests were successful in detecting the horizon. However, this sensor was only tested on an Arduino Uno R3 board, using a specific library from Adafruit written in C++. Tests on the MSP430 Launchpad could not be performed due to the lockdown.

Moreover, further tests need to be done to measure the precision of the resulting values α and β and determine if the resolution provided by an 8x8 grid is enough.

IX.1.4. Communication with the central unit
The communication protocol between the microcontroller and the central unit is functional. As of now, four commands are implemented, with one command accepting one parameter. More specifications on the central unit could require adding more commands to the command set. This can be done easily as the code structure that handles commands on the microcontroller is flexible. However, the code should be tested with a network of sensors using a MSP430FR59XX microcontroller that has multiple hardware I2C modules.

30 | Polytech'Nice Sophia, Département électronique Les Templiers 930 Route des Colles - BP 145 06903 Sophia Antipolis Cedex

IX.1.5. PCB
We managed to complete one working prototype validating the following requirements:
- The power output
- The circuit protection of solar cells
The other hardware requirements were not tested but the groundwork is already done. The PCB layout of a nearly full featured board is ready to be printed and tested. The layout was checked by the website JLCPCB (https://jlcpcb.com/) and deemed as sound.

## IX.2. Parts that require further work

IX.2.1. Using the ultra-low power features of the microcontroller
We were not able to measure the consumption of the microcontroller when it is in function. We also did not exploit the low-power modes in our prototypes, as we wanted to make the design functional before trying to reduce power consumption. However, the environment we used to develop our code, Code Composer Studio, has an “Optimization advice” feature that helps reduce power consumption and optimize computation time. Once we have a working prototype, we can quickly optimize power consumption using this feature

IX.2.2. 32x24 Thermal camera
As mentioned above, the 8x8 camera is functional but might not meet our requirements regarding precision. We attempted to use the 32x24 MLX90640 camera and tried prototyping using an Arduino library from Adafruit. However, the program for that camera could not be tested due to memory limitations. The temporary storage that we need for the linear regression algorithm is taking too much space. To use this camera, we would need to write the sensor interfacing program in C and tweak the algorithm so that it uses less temporary storage.

IX.2.3. Solar sensors
We could not design a program to test the solar sensors due to a lack of time. This part needs to be developed as it is an essential sensor to determine the orientation of the satellite.

IX.2.4.Network of sensors
We need to write a program that can read data from multiple sensors on the same I2C bus. We would only need to combine the programs that read one sensor, and make sure each address is assigned to only one sensor. Furthermore, we need to test the sensor network when the microcontroller also communicates with the central unit. We want to make sure that reading and processing the sensor values is fast enough to provide real-time reading to the central unit.

31 | Polytech'Nice Sophia, Département électronique Les Templiers 930 Route des Colles - BP 145 06903 Sophia Antipolis Cedex

# X.References

You can find all datasheets and source documents, as well as original Kicad design and Arduino code on the Github of this project.
https://github.com/RomainCocogne/NanoSat.git

Other links:

Texas Instrument, “MSP430FR599x, MSP430FR596x Mixed-Signal Microcontrollers datasheet”, [SLASE54C]

https://www.ti.com/lit/ds/symlink/msp430fr5949.pdf?ts=1590224343299

Texas Instruments, “MSP430FR58xx, MSP430FR59xx, and MSP430FR6xx Family User Guide”, [SLAU367P]
https://www.ti.com/lit/ug/slau367p/slau367p.pdf?ts=1590224617008

Texas Instruments; “Using the USCI I2C Master” [SLAA382A]

http://www.ti.com/lit/an/slaa382a/slaa382a.pdf

Texas Instruments; “Using the USCI I2C Slave” [SLAA383]

https://datasheet.datasheetarchive.com/originals/library/Datasheet-080/DASF004576.pdf

CubeSat design specification

https://static1.squarespace.com/static/5418c831e4b0fa4ecac1bacd/t/56e9b62337013b6c063a655a/1458157095454/cds_rev13_final2.pdf (https://static1.squarespace.com/static/5418c831e4b0fa4ecac1bacd/t/56e9b62337013b6c063a655a/1458157095454/cds_rev13_final2.pdf)

TrisolX layout

https://d3i71xaburhd42.cloudfront.net/6ffac9621ad9e26aa4264a1be23f66f674bda921/10-Figure14-1.png

GOMspace nanopower p31u, Power supply

https://gomspace.com/UserFiles/Subsystems/datasheet/gs-ds-nanopower-p31u-27.pdf

32 | Polytech'Nice Sophia, Département électronique Les Templiers 930 Route des Colles - BP 145 06903 Sophia Antipolis Cedex

# XI.Annexes

## XI.1.Code

XI.1.1.Thermal Camera

Figure XI.1. Main test code AMG8833, part 1

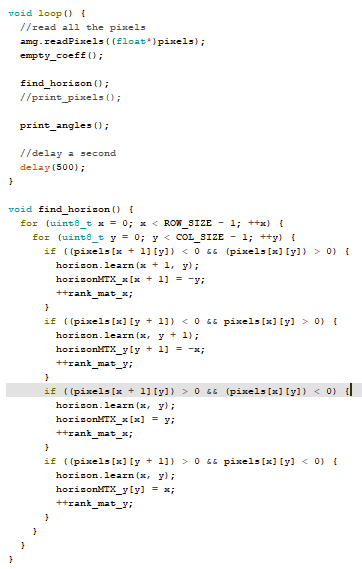
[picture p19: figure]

33 | Polytech'Nice Sophia, Département électronique Les Templiers 930 Route des Colles - BP 145 06903 Sophia Antipolis Cedex

Figure XI.2. Main test code AMG8833, part 2

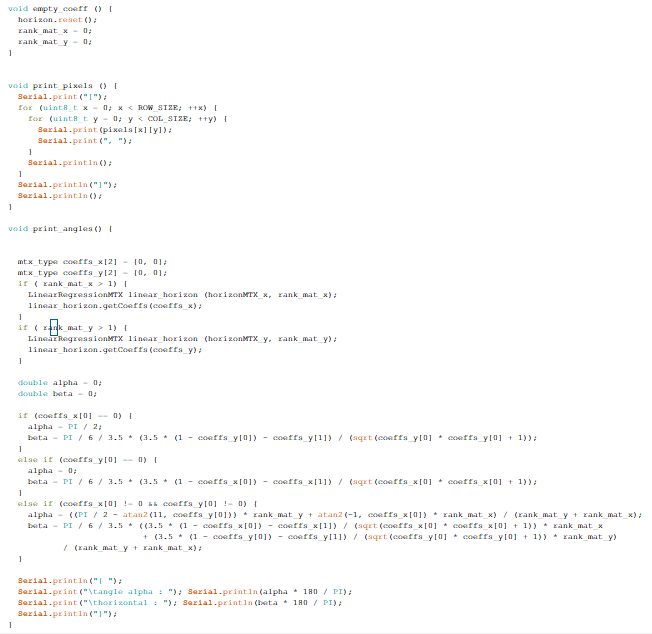
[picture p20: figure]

34 | Polytech'Nice Sophia, Département électronique Les Templiers 930 Route des Colles - BP 145 06903 Sophia Antipolis Cedex

Figure XI.3. Main test code AMG8833, part 3

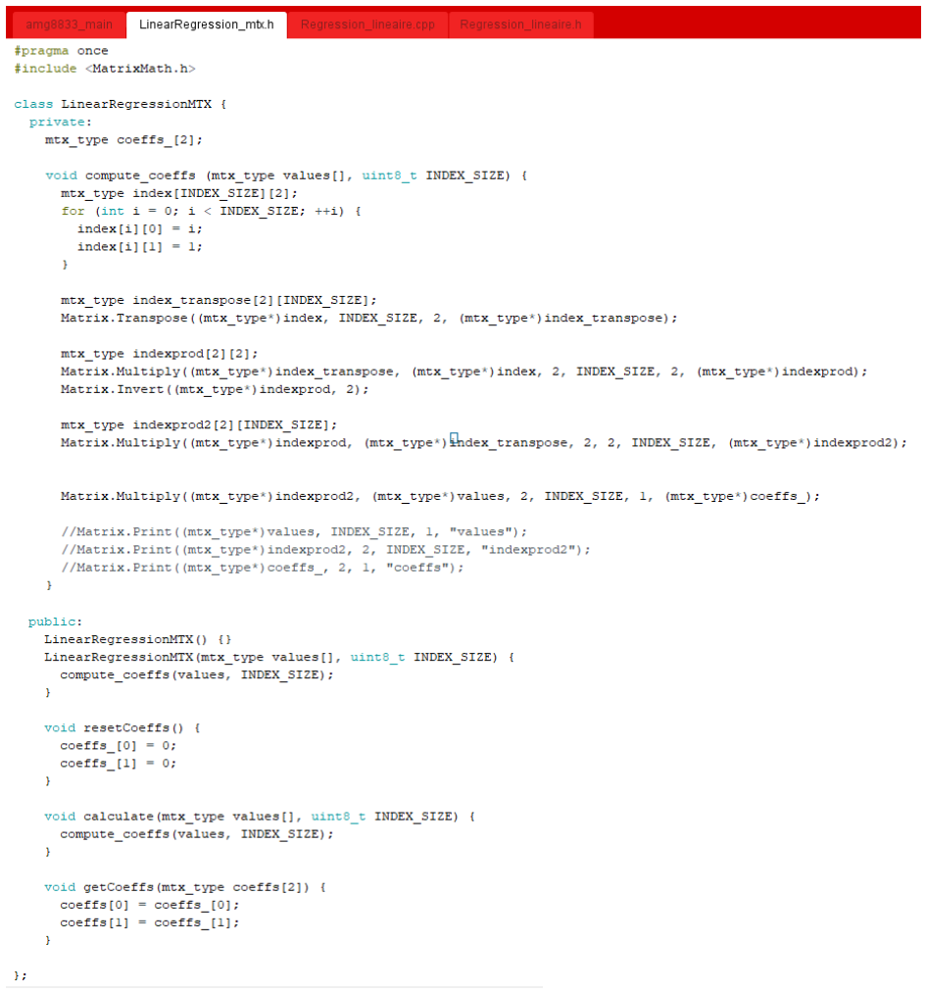
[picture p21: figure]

35 | Polytech'Nice Sophia, Département électronique Les Templiers 930 Route des Colles - BP 145 06903 Sophia Antipolis Cedex

Figure XI.4. Linear Regression class test code AMG8833

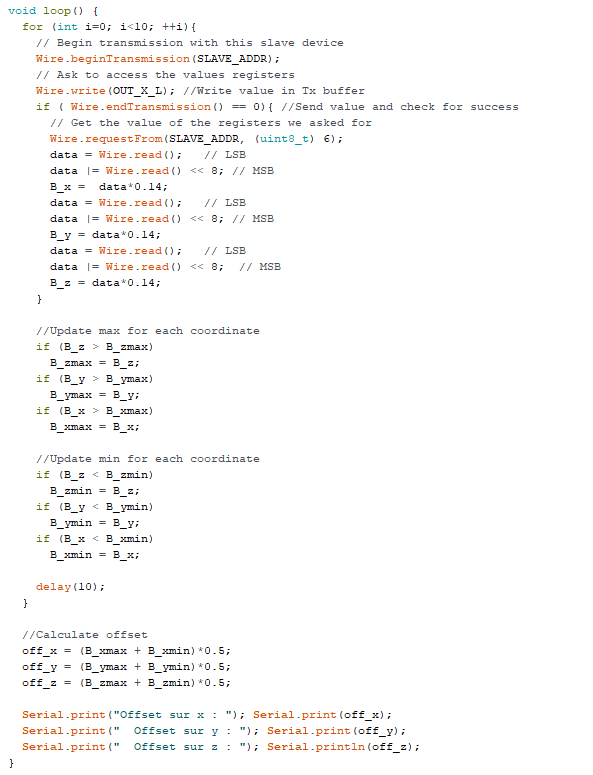
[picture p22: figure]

36 | Polytech'Nice Sophia, Département électronique Les Templiers 930 Route des Colles - BP 145 06903 Sophia Antipolis Cedex

XI.1.2.Magnetic sensor calibration

Figure XI.5 Calibration program for the LSM9DS1 magnetic sensor

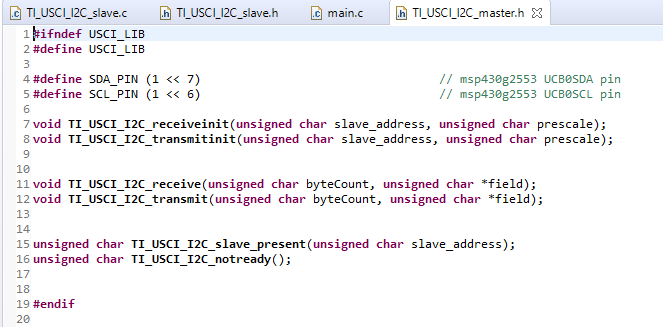
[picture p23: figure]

37 | Polytech'Nice Sophia, Département électronique Les Templiers 930 Route des Colles - BP 145 06903 Sophia Antipolis Cedex

XI.1.3. USCI_I2C library

XI.1.3.1. USCI_I2C_master library

Figure XI.6 USCI_I2C_master library interface

Functional description of the library:

TI_USCI_I2C_receiveinit: Configures the I2C module in receiver mode to receive a message from a slave
TI_USCI_I2C_transmitinit: Configures the I2C module in transmitter mode to send a message to a slave

TI_USCI_I2C_receive: Stores byteCount received bytes at the memory space pointed by field TI_USCI_I2C_transmit: Transmits byteCount bytes from the memory space pointed by field

TI_USCI_I2C_slave_present: Checks if the address slave_address corresponds to a slave on the bus. TI_USCI_I2C_not_ready: Checks if the bus is busy

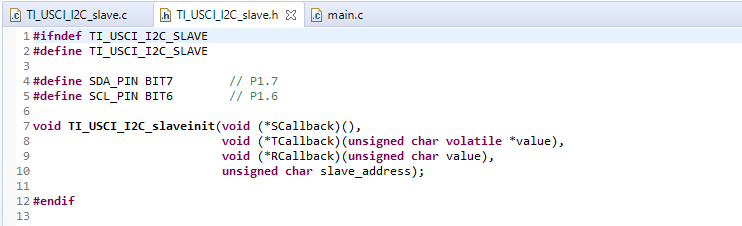
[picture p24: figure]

38 | Polytech'Nice Sophia, Département électronique Les Templiers 930 Route des Colles - BP 145 06903 Sophia Antipolis Cedex

XI.1.3.2.USCI_I2C_slave library

Figure XI.7 USCI_I2C_slave library interface

Functional description of the library:

TI_USCI_I2C_slavetinit: Initializes the I2C module in slave mode with the address slave_address.
- SCallback: function called when a start condition is detected on the bus
- TCallback: function called for every byte of data requested by the master
- RCallback: function called for every byte of data received from the master

39 | Polytech'Nice Sophia, Département électronique Les Templiers 930 Route des Colles - BP 145 06903 Sophia Antipolis Cedex

## XI.2.Schematics

XI.2.1.Prototype 2

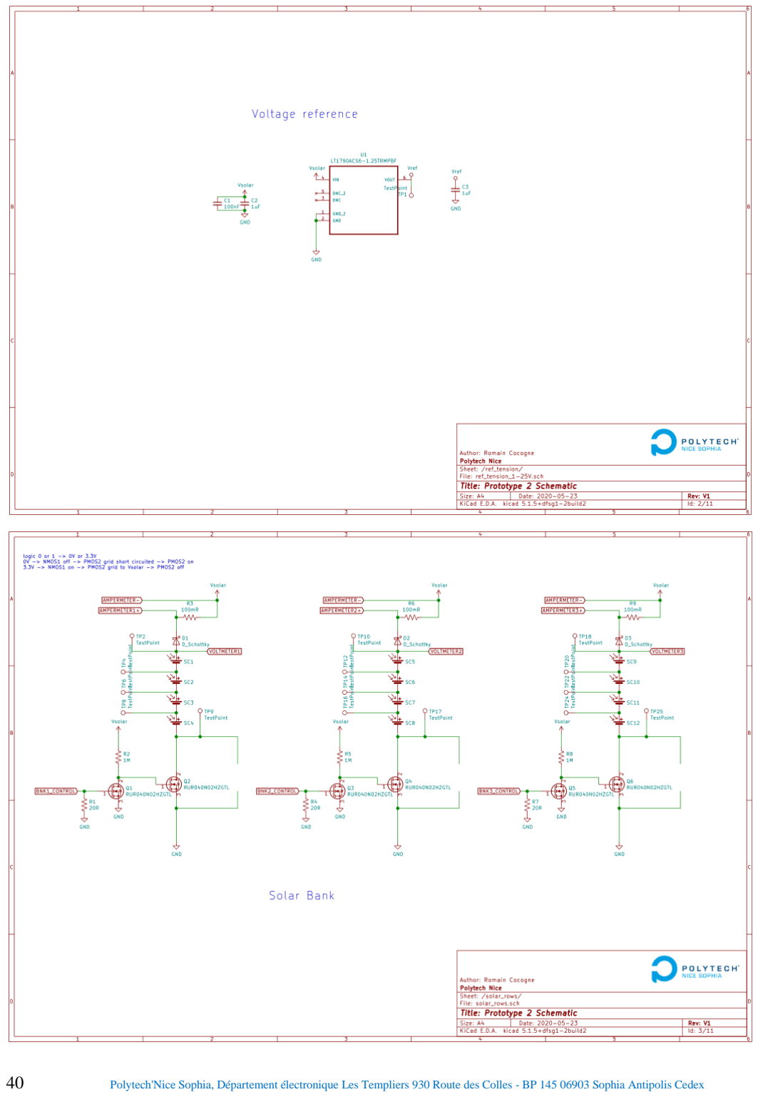
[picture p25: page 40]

40 | Polytech'Nice Sophia, Département électronique Les Templiers 930 Route des Colles - BP 145 06903 Sophia Antipolis Cedex

41 | Polytech'Nice Sophia, Département électronique Les Templiers 930 Route des Colles - BP 145 06903 Sophia Antipolis Cedex

42 | Polytech'Nice Sophia, Département électronique Les Templiers 930 Route des Colles - BP 145 06903 Sophia Antipolis Cedex

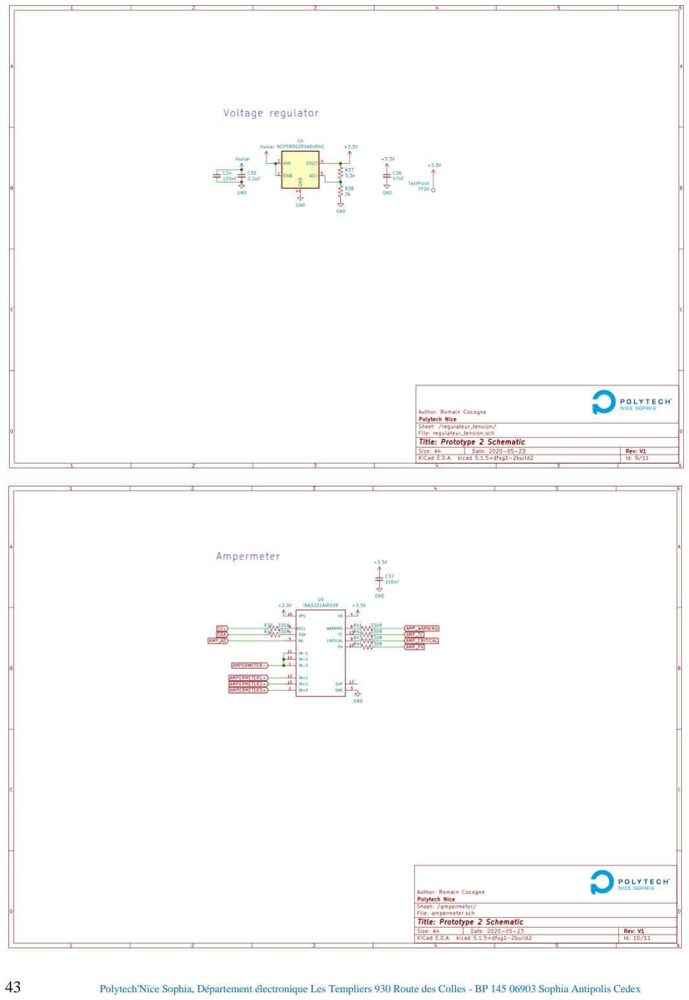
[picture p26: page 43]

43 | Polytech'Nice Sophia, Département électronique Les Templiers 930 Route des Colles - BP 145 06903 Sophia Antipolis Cedex

44 | Polytech'Nice Sophia, Département électronique Les Templiers 930 Route des Colles - BP 145 06903 Sophia Antipolis Cedex

Figure XI.2. Second prototype schematic

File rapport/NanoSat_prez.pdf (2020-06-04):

# INTELLIGENT SOLAR PANEL FOR CUBESAT

# Brunin Camille, Combal Quentin, Romain Cocogne 2019-2020


# Tutor: Florentin Millour, Lab Lagrange

# SUMMARY


# - Introduction - Requirements - Architecture - Planning - Development - Setbacks - Challenges - Conclusion

INTELLIGENT SOLAR PANEL FOR CUBESAT | Brunin Camille Combal Quentin Romain Cocogne | Polytech Nice, 2019-2020 | 2

# INTRODUCTION


INTELLIGENT SOLAR PANEL FOR CUBESAT | Brunin Camille Combal Quentin Romain Cocogne | Polytech Nice, 2019-2020 | 3

# FULL SYSTEM OVERVIEW

Earth station

INTELLIGENT SOLAR PANEL FOR CUBESAT | Brunin Camille Combal Quentin Romain Cocogne | Polytech Nice, 2019-2020 | 4


# - Design a solar panel that can power the satellite - Design a power management system - Perform measurements to determine the satellite’s orientation - Send the measurements to an on-board central unit

# ➢Design a power efficient system

# REQUIREMENTS

INTELLIGENT SOLAR PANEL FOR CUBESAT | Brunin Camille Combal Quentin Romain Cocogne | Polytech Nice, 2019-2020 | 5

# ARCHITECTURE


INTELLIGENT SOLAR PANEL FOR CUBESAT | Brunin Camille Combal Quentin Romain Cocogne | Polytech Nice, 2019-2020 | 6

# SYSTEM INTERACTION WITH ENVIRONMENT

INTELLIGENT SOLAR PANEL FOR CUBESAT | Brunin Camille Combal Quentin Romain Cocogne | Polytech Nice, 2019-2020 | 7

# PLANNING – FIRST SEMESTER


INTELLIGENT SOLAR PANEL FOR CUBESAT | Brunin Camille Combal Quentin Romain Cocogne | Polytech Nice, 2019-2020 | 8

# PLANNING – SECOND SEMESTER


INTELLIGENT SOLAR PANEL FOR CUBESAT | Brunin Camille Combal Quentin Romain Cocogne | Polytech Nice, 2019-2020 | 9

# SENSORS SPECIFICATIONS


INTELLIGENT SOLAR PANEL FOR CUBESAT | Brunin Camille Combal Quentin Romain Cocogne | Polytech Nice, 2019-2020 | 10

# Earth station

N | S

# DEVELOPMENT – SENSOR NETWORK

I²C BUS; MSP430

INTELLIGENT SOLAR PANEL FOR CUBESAT | Brunin Camille Combal Quentin Romain Cocogne | Polytech Nice, 2019-2020 | 11

# ENERGIA IDE with “Wire” library: - High level, hides hardware detail - Not very optimized

# Code Composer Studio with firmware: - Highly efficient, more control over hardware - Few libraries, longer development time

# LM75A

# AMG8833 LSM9DS1

# MLX90640

# DEVELOPMENT – SOLAR PANEL

Earth station

INTELLIGENT SOLAR PANEL FOR CUBESAT | Brunin Camille Combal Quentin Romain Cocogne | Polytech Nice, 2019-2020 | 14

# DEVELOPMENT – SOLAR PANEL

INTELLIGENT SOLAR PANEL FOR CUBESAT; Brunin Camille Combal Quentin Romain Cocogne; Polytech Nice, 2019-2020; Prototype #1

# DEVELOPMENT – UNPLANNED MODIFICATIONS


INTELLIGENT SOLAR PANEL FOR CUBESAT | Brunin Camille Combal Quentin Romain Cocogne | Polytech Nice, 2019-2020 | 16

# Prototype #2

Zener diode | LT1790ACS6-1.25
Shunt resistor | INA3221

# TECHNOLOGICAL CHALLENGES


INTELLIGENT SOLAR PANEL FOR CUBESAT | Brunin Camille Combal Quentin Romain Cocogne | Polytech Nice, 2019-2020 | 18

# - Setting up an efficient progrmamingenvironment

# - Adapting to a change of microcontroller

MSP-EXP430FR5739 | MSP-EXP430G2
ENERGIA | CODE COMPOSER STUDIO

# TECHNOLOGICAL CHALLENGES


INTELLIGENT SOLAR PANEL FOR CUBESAT | Brunin Camille Combal Quentin Romain Cocogne | Polytech Nice, 2019-2020 | 19

# SETBACKS – CONSEQUENCES OF COVID-19


INTELLIGENT SOLAR PANEL FOR CUBESAT | Brunin Camille Combal Quentin Romain Cocogne | Polytech Nice, 2019-2020 | 20

# SETBACKS – CHANGE OF PLANS


INTELLIGENT SOLAR PANEL FOR CUBESAT | Brunin Camille Combal Quentin Romain Cocogne | Polytech Nice, 2019-2020 | 21

# CONCLUSION – THE PROJECT SO FAR

INTELLIGENT SOLAR PANEL FOR CUBESAT; Brunin Camille Combal Quentin Romain Cocogne; Polytech Nice, 2019-2020

• Design a solar panel that can power the satellite
• Design a power management system
• Cut-off system → Simulated
• Current and Voltage measurements → Missing components
• Temperature measurements
• Perform measurements to determine the satellite’s orientation
• Magnetic sensor integration
• Thermal Camera integration → Need to adapt the algorithm
• Solar sensors integration
• Send the measurements to an on-board central unit

# CONCLUSION – FURTHER WORK

INTELLIGENT SOLAR PANEL FOR CUBESAT | Brunin Camille Combal Quentin Romain Cocogne | Polytech Nice, 2019-2020 | 23

# - Learn to exploit the low-power capabilities of the microcontroller

# - Use Code Composer Studio (CCS) tools

# - Rework the algorithm for the thermal camera

- Make it work with the 32x24 camera.

# - Work with the solar sensor

# - Groundwork done with other sensors

# - Make a prototype with the full network of sensors

# - Performance analysis of the full system

- http://univ-cotedazur.fr/en/idex/academies/space-environment-risk-and-resilience/contents/projects/a-satellite-for-the-uca

# - https://www.ti.com/tool/CCSTUDIO

# - https://scienceprog.com/msp-exp430fr5739-board-have-just-arrived/

# SOURCES

INTELLIGENT SOLAR PANEL FOR CUBESAT | Brunin Camille Combal Quentin Romain Cocogne | Polytech Nice, 2019-2020 | 24

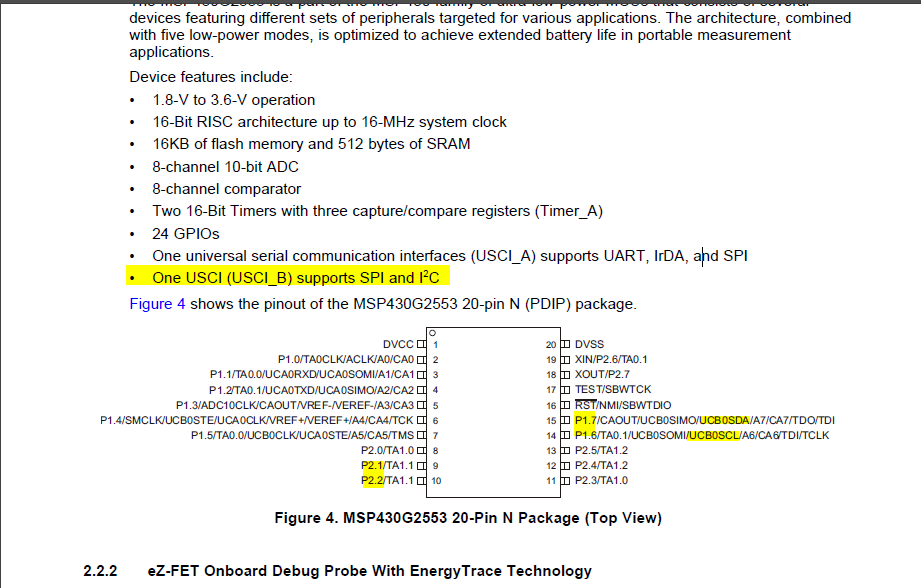
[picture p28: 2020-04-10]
datasheets/MSPEXP430/MSP430G2553_true_pinout.png

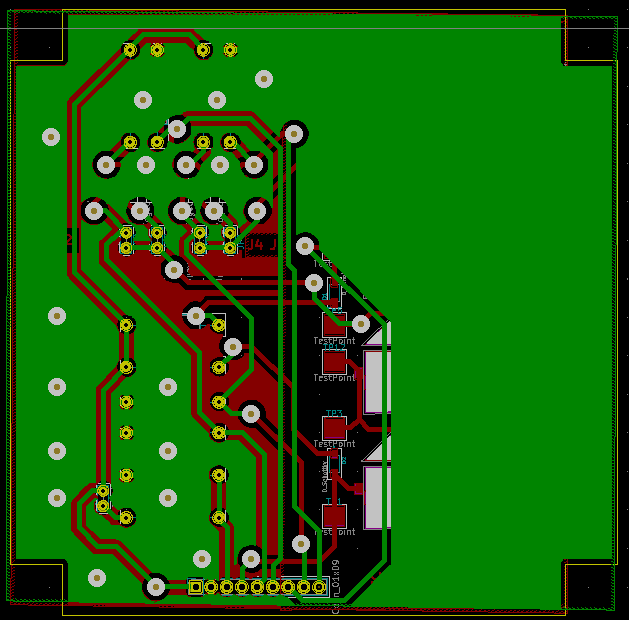
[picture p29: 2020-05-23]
kicad/proto2/proto2/gerber/proto1_BCU.png

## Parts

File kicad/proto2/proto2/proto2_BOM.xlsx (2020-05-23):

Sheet: Feuil1
Item | Qty | Reference(s) | Value | Datasheet
1 | 1 | AC1 | LSM9DS1TR | http://www.st.com/content/ccc/resource/technical/document/datasheet/1e/3f/2a/d6/25/eb/48/46/DM00103319.pdf/files/DM00103319.pdf/jcr:content/translations/en.DM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
2 | 14 | C1, C5, C7, C23, C24, C25, C26, C28, C30, C31, C32, C33, C34, C37 | 100nF | ~
3 | 2 | C2, C3 | 1uF | ~
4 | 6 | C4, C8, C9, C10, C11, C29 | 10uF | ~
5 | 5 | C12, C13, C14, C15, C27 | 10nF | ~
6 | 1 | C22 | 2.2nF | ~
7 | 1 | C35 | 2.2uF | ~
8 | 1 | C36 | 47nF | ~
9 | 3 | D1, D2, D3 | D_Schottky | ~
10 | 1 | IC1 | MLX90641ESF-BAA-000-TU | https://www.mouser.com/datasheet/2/734/MLX90614-Datasheet-Melexis-953298.pdf
11 | 1 | IC2 | PCT2075DP,118 | http://www.nxp.com/docs/en/data-sheet/PCT2075.pdf
12 | 1 | IC3 | MSP430FR5964IPNR | http://www.ti.com/general/docs/suppproductinfo.tsp?distId=10
13 | 1 | J5 | HEADER_2x7_2.54MM
14 | 1 | J6 | 532610871 | ~
15 | 14 | Q1, Q2, Q3, Q4, Q5, Q6, Q7, Q8, Q9, Q10, Q11, Q12, Q13, Q14 | RUR040N02HZGTL | ~
16 | 7 | R1, R4, R7, R10, R14, R29, R31 | 20R | ~
17 | 7 | R2, R5, R8, R11, R15, R30, R32 | 1M | ~
18 | 3 | R3, R6, R9 | 100mR
19 | 13 | R12, R13, R16, R17, R18, R27, R28, R39, R40, R41, R42, R43, R44 | 330R
20 | 1 | R19 | 47kR
21 | 11 | R20, R21, R22, R23, R24, R25, R26, R33, R34, R35, R36 | 10k
22 | 1 | R37 | 3.3k
23 | 1 | R38 | 2k
24 | 12 | SC1, SC2, SC3, SC4, SC5, SC6, SC7, SC8, SC9, SC10, SC11, SC12 | Solar_Cell | ~
25 | 1 | SW1 | BP_DROIT_TRAV-switch
26 | 1 | U1 | LT1790ACS6-1.25TRMPBF | LT1790ACS6-1.25#TRMPBF
27 | 2 | U2, U3 | S3274-05
28 | 1 | U4 | NCP59302DSADJR4G | http://ww1.microchip.com/downloads/en/DeviceDoc/MCP14A0303_4_5-Data-Sheet-20006046A.pdf
29 | 1 | U5 | INA3221AIRGVR | Texas Instruments

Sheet: proto2
Source:,/home/romain/Bureau/NanoSat/kicad/proto2/proto2/proto2.sch,,,
Date:,sam. 23 mai 2020 21:53:54,,,
Tool:,Eeschema 5.1.5+dfsg1-2build2,,,
Generator:,/usr/share/kicad/plugins/bom_csv_grouped_by_value.py,,,
Component Count:,115,,,
,,,,
Individual Components:,,,,
,,,,
Item,Qty,Reference(s),Value,Datasheet
,,AC1,LSM9DS1TR,http://www.st.com/content/ccc/resource/technical/document/datasheet/1e/3f/2a/d6/25/eb/48/46/DM00103319.pdf/files/DM00103319.pdf/jcr:content/translations/en.DM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
,,C1,100nF,~
,,C2,1uF,~
,,C3,1uF,~
,,C4,10uF,~
,,C5,100nF,~
,,C7,100nF,~
,,C8,10uF,~
,,C9,10uF,~
,,C10,10uF,~
,,C11,10uF,~
,,C12,10nF,~
,,C13,10nF,~
,,C14,10nF,~
,,C15,10nF,~
,,C22,2.2nF,~
,,C23,100nF,~
,,C24,100nF,~
,,C25,100nF,~
,,C26,100nF,~
,,C27,10nF,~
,,C28,100nF,~
,,C29,10uF,~
,,C30,100nF,~
,,C31,100nF,~
,,C32,100nF,~
,,C33,100nF,~
,,C34,100nF,~
,,C35,2.2uF,~
,,C36,47nF,~
,,C37,100nF,~
,,D1,D_Schottky,~
,,D2,D_Schottky,~
,,D3,D_Schottky,~
,,IC1,MLX90641ESF-BAA-000-TU,https://www.mouser.com/datasheet/2/734/MLX90614-Datasheet-Melexis-953298.pdf
,,IC2,"PCT2075DP,118",http://www.nxp.com/docs/en/data-sheet/PCT2075.pdf
,,IC3,MSP430FR5964IPNR,http://www.ti.com/general/docs/suppproductinfo.tsp?distId=10
,,J5,HEADER_2x7_2.54MM,
,,J6,532610871,3.4mm
,,Q1,RUR040N02HZGTL,~
,,Q2,RUR040N02HZGTL,~
,,Q3,RUR040N02HZGTL,~
,,Q4,RUR040N02HZGTL,~
,,Q5,RUR040N02HZGTL,~
,,Q6,RUR040N02HZGTL,~
,,Q7,RUR040N02HZGTL,~
,,Q8,RUR040N02HZGTL,~
,,Q9,RUR040N02HZGTL,~
,,Q10,RUR040N02HZGTL,~
,,Q11,RUR040N02HZGTL,~
,,Q12,RUR040N02HZGTL,~
,,Q13,RUR040N02HZGTL,~
,,Q14,RUR040N02HZGTL,~
,,R1,20R,~
,,R2,1M,~
,,R3,100mR,
,,R4,20R,~
,,R5,1M,~
,,R6,100mR,
,,R7,20R,~
,,R8,1M,~
,,R9,100mR,
,,R10,20R,~
,,R11,1M,~
,,R12,330R,
,,R13,330R,
,,R14,20R,~
,,R15,1M,~
,,R16,330R,
,,R17,330R,
,,R18,330R,
,,R19,47kR,
,,R20,10k,
,,R21,10k,
,,R22,10k,
,,R23,10k,
,,R24,10k,
,,R25,10k,
,,R26,10k,
,,R27,330R,
,,R28,330R,
,,R29,20R,~
,,R30,1M,~
,,R31,20R,~
,,R32,1M,~
,,R33,10k,
,,R34,10k,
,,R35,10k,
,,R36,10k,
,,R37,3.3k,
,,R38,2k,
,,R39,330R,
,,R40,330R,
,,R41,330R,
,,R42,330R,
,,R43,330R,
,,R44,330R,
,,SC1,Solar_Cell,~
,,SC2,Solar_Cell,~
,,SC3,Solar_Cell,~
,,SC4,Solar_Cell,~
,,SC5,Solar_Cell,~
,,SC6,Solar_Cell,~
,,SC7,Solar_Cell,~
,,SC8,Solar_Cell,~
,,SC9,Solar_Cell,~
,,SC10,Solar_Cell,~
,,SC11,Solar_Cell,~
,,SC12,Solar_Cell,~
,,SW1,BP_DROIT_TRAV-switch,
,,U1,LT1790ACS6-1.25TRMPBF,LT1790ACS6-1.25#TRMPBF
,,U2,S3274-05,
,,U3,S3274-05,
,,U4,NCP59302DSADJR4G,http://ww1.microchip.com/downloads/en/DeviceDoc/MCP14A0303_4_5-Data-Sheet-20006046A.pdf
,,U5,INA3221AIRGVR,Texas Instruments
,,,,
,,,,
,,,,
Collated Components:,,,,
,,,,
Item,Qty,Reference(s),Value,Datasheet
1,1,AC1,LSM9DS1TR,http://www.st.com/content/ccc/resource/technical/document/datasheet/1e/3f/2a/d6/25/eb/48/46/DM00103319.pdf/files/DM00103319.pdf/jcr:content/translations/en.DM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
2,14,"C1, C5, C7, C23, C24, C25, C26, C28, C30, C31, C32, C33, C34, C37",100nF,~
3,2,"C2, C3",1uF,~
4,6,"C4, C8, C9, C10, C11, C29",10uF,~
5,5,"C12, C13, C14, C15, C27",10nF,~
6,1,C22,2.2nF,~
7,1,C35,2.2uF,~
8,1,C36,47nF,~
9,3,"D1, D2, D3",D_Schottky,~
10,1,IC1,MLX90641ESF-BAA-000-TU,https://www.mouser.com/datasheet/2/734/MLX90614-Datasheet-Melexis-953298.pdf
11,1,IC2,"PCT2075DP,118",http://www.nxp.com/docs/en/data-sheet/PCT2075.pdf
12,1,IC3,MSP430FR5964IPNR,http://www.ti.com/general/docs/suppproductinfo.tsp?distId=10
13,1,J5,HEADER_2x7_2.54MM,
14,1,J6,532610871,3.4mm
15,14,"Q1, Q2, Q3, Q4, Q5, Q6, Q7, Q8, Q9, Q10, Q11, Q12, Q13, Q14",RUR040N02HZGTL,~
16,7,"R1, R4, R7, R10, R14, R29, R31",20R,~
17,7,"R2, R5, R8, R11, R15, R30, R32",1M,~
18,3,"R3, R6, R9",100mR,
19,13,"R12, R13, R16, R17, R18, R27, R28, R39, R40, R41, R42, R43, R44",330R,
20,1,R19,47kR,
21,11,"R20, R21, R22, R23, R24, R25, R26, R33, R34, R35, R36",10k,
22,1,R37,3.3k,
23,1,R38,2k,
24,12,"SC1, SC2, SC3, SC4, SC5, SC6, SC7, SC8, SC9, SC10, SC11, SC12",Solar_Cell,~
25,1,SW1,BP_DROIT_TRAV-switch,
26,1,U1,LT1790ACS6-1.25TRMPBF,LT1790ACS6-1.25#TRMPBF
27,2,"U2, U3",S3274-05,
28,1,U4,NCP59302DSADJR4G,http://ww1.microchip.com/downloads/en/DeviceDoc/MCP14A0303_4_5-Data-Sheet-20006046A.pdf
29,1,U5,INA3221AIRGVR,Texas Instruments

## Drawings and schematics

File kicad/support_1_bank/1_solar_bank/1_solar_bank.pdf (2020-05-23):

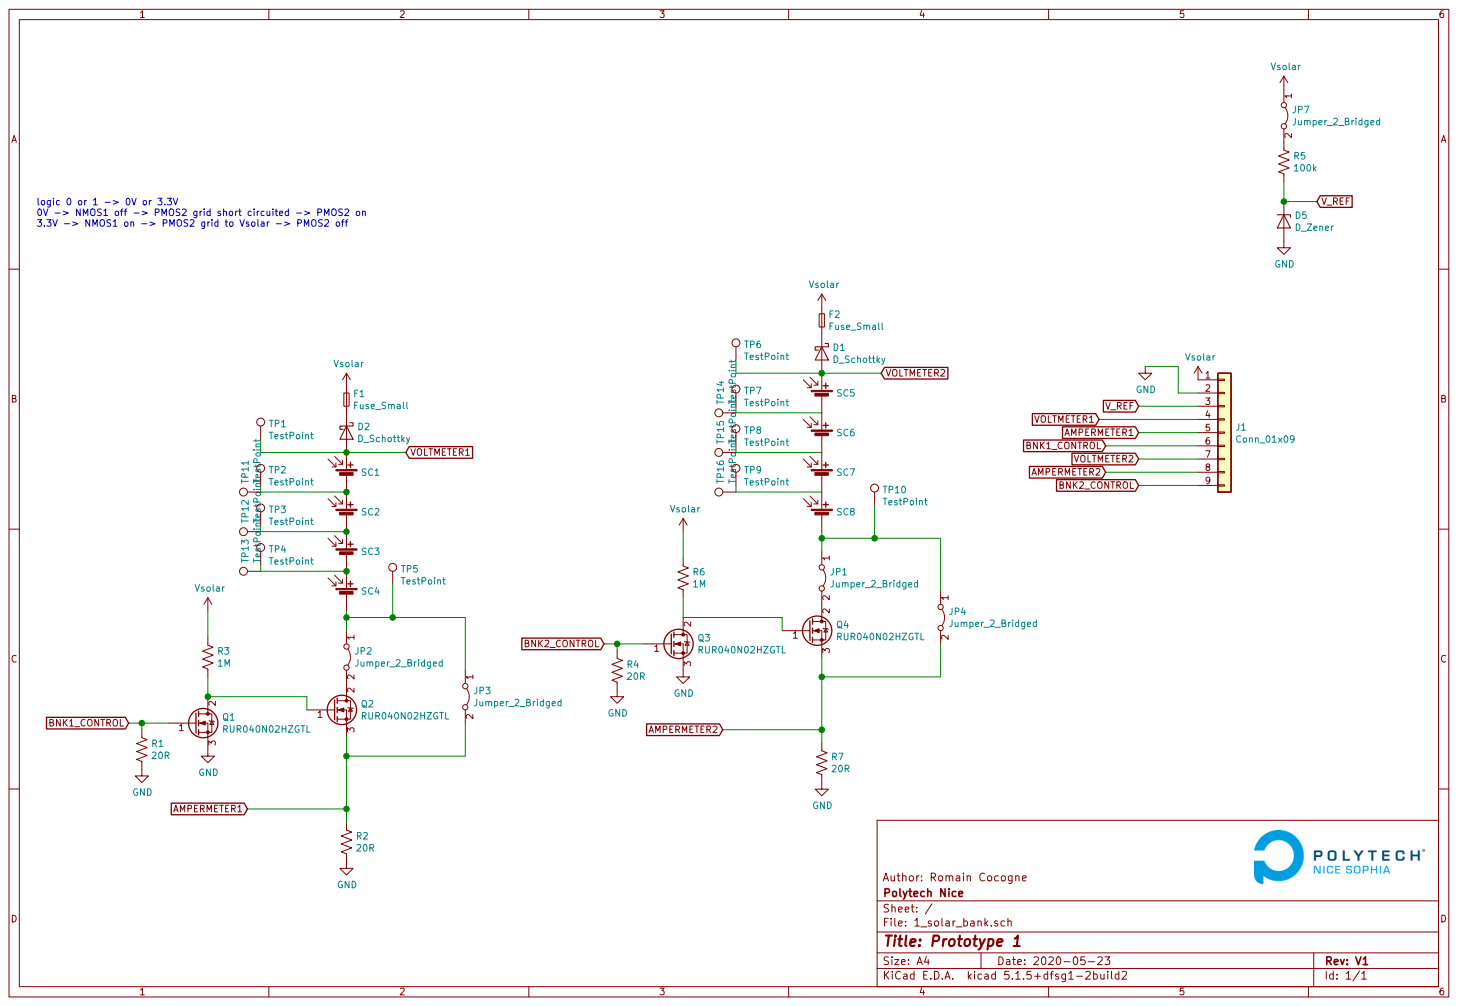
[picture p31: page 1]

logic 0 or 1 -> 0V or 3.3V
0V -> NMOS1 off -> PMOS2 grid short circuited -> PMOS2 on
3.3V -> NMOS1 on -> PMOS2 grid to Vsolar -> PMOS2 off

Author: Romain Cocogne SC8 GND GND

File: 1_solar_bank.sch Sheet: / Polytech Nice

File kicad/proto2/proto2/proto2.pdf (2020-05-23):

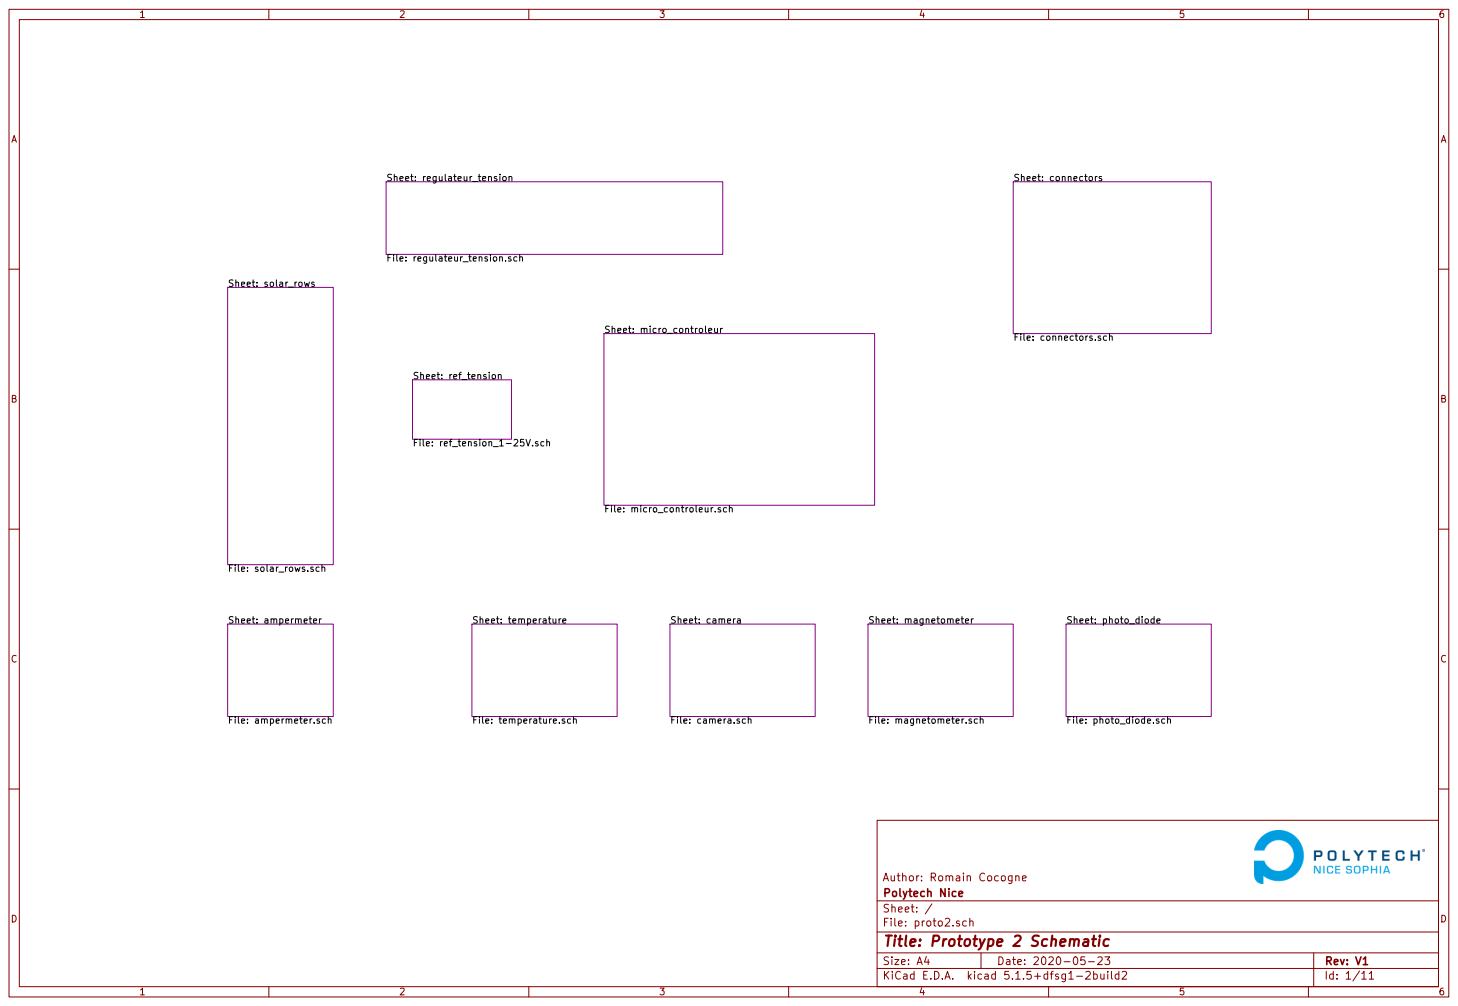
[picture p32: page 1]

Sheet: connectors File: connectors.sch

Author: Romain Cocogne
File: proto2.sch Sheet: / Polytech Nice

Id: 1/11 Title: Prototype 2 Schematic

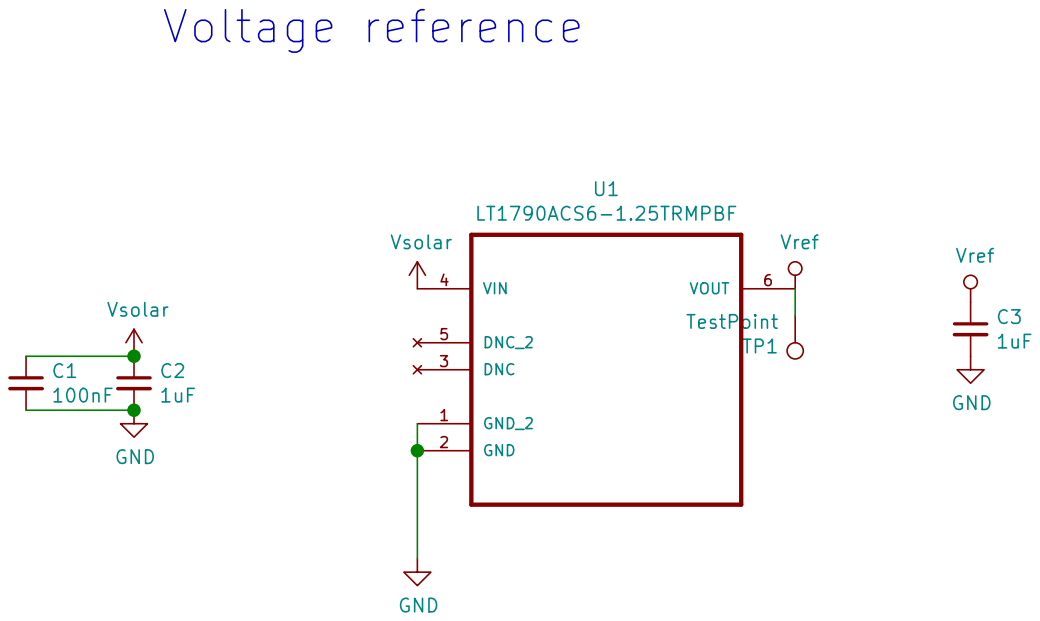
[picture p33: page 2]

Author: Romain Cocogne GND

Polytech Nice
Sheet: /ref_tension/
File: ref_tension_1-25V.sch
Id: 2/11 Title: Prototype 2 Schematic

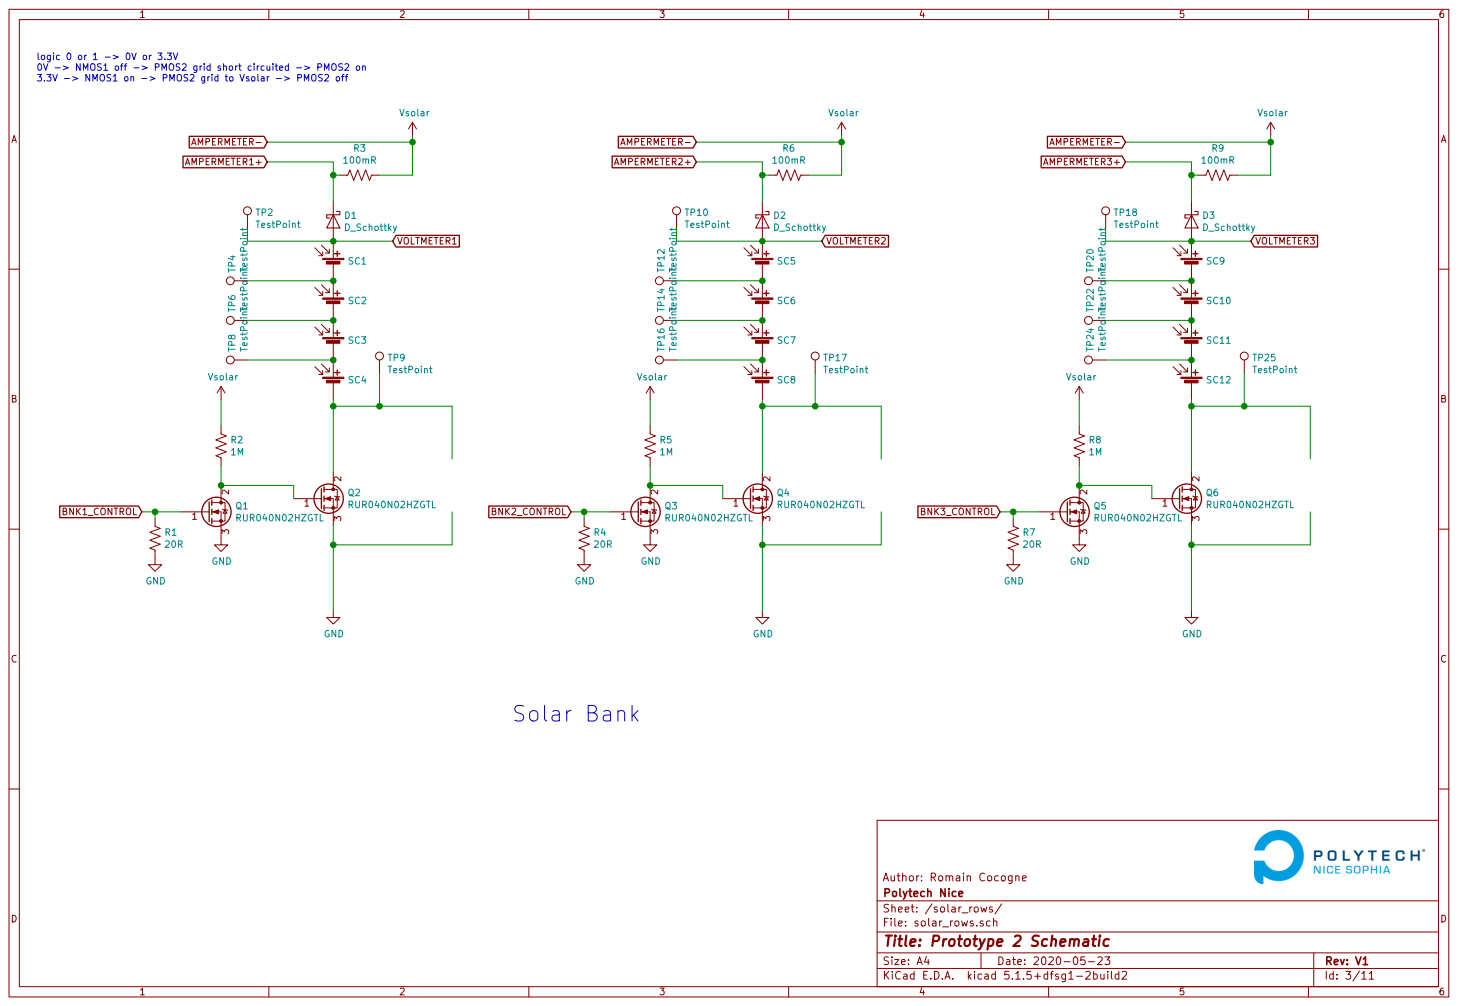
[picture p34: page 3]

logic 0 or 1 -> 0V or 3.3V
0V -> NMOS1 off -> PMOS2 grid short circuited -> PMOS2 on
3.3V -> NMOS1 on -> PMOS2 grid to Vsolar -> PMOS2 off

2 3 Q3RUR040N02HZGTL TP17 TestPoint TP12 TestPoint TP14 TestPoint TP16 TestPoint TP24 TestPointTP22 TestPointTP20 TestPoint

Author: Romain Cocogne
Polytech Nice
Sheet: /solar_rows/
File: solar_rows.sch
Id: 3/11 Title: Prototype 2 Schematic

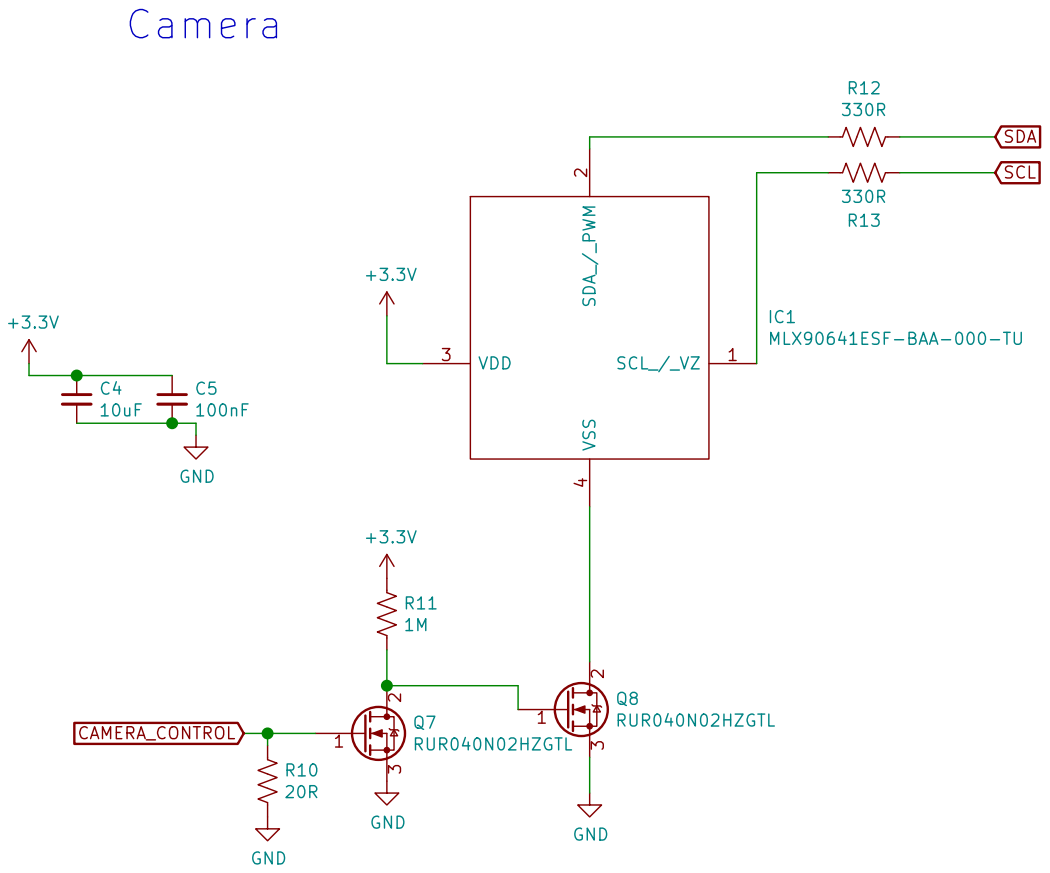
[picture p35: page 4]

Author: Romain Cocogne
File: camera.sch Sheet: /camera/ Polytech Nice

Id: 4/11 Title: Prototype 2 Schematic

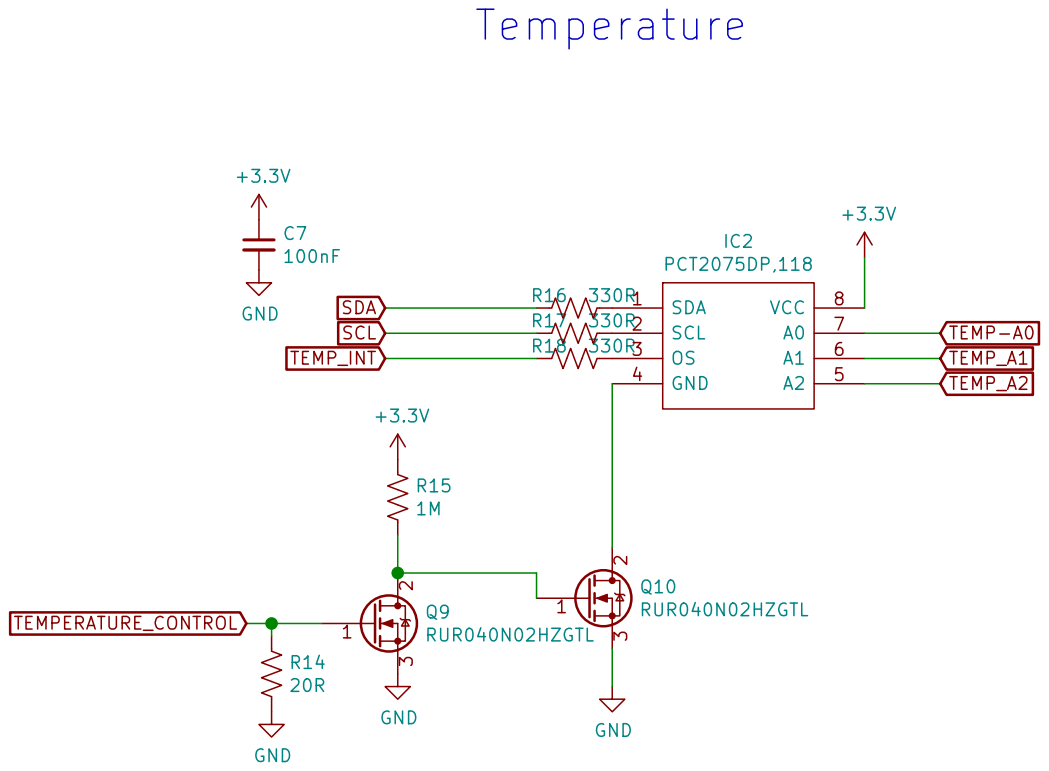
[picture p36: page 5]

Author: Romain Cocogne
Polytech Nice
Sheet: /temperature/
File: temperature.sch
Id: 5/11 Title: Prototype 2 Schematic

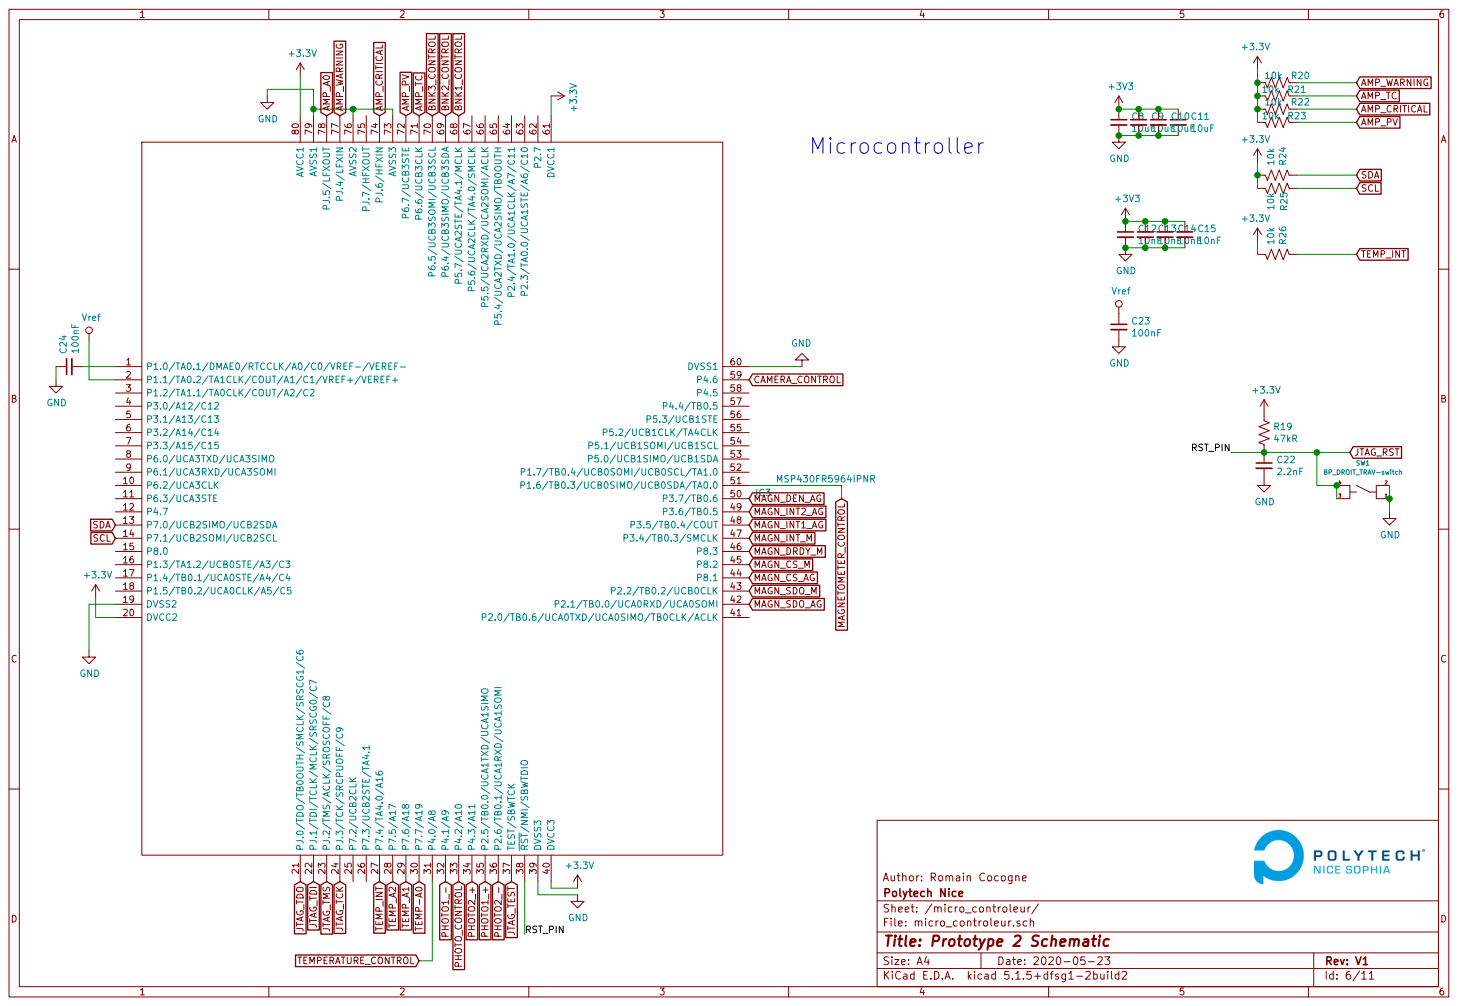
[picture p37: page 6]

Author: Romain Cocogne
Polytech Nice
Sheet: /micro_controleur/
File: micro_controleur.sch
Id: 6/11 Title: Prototype 2 Schematic

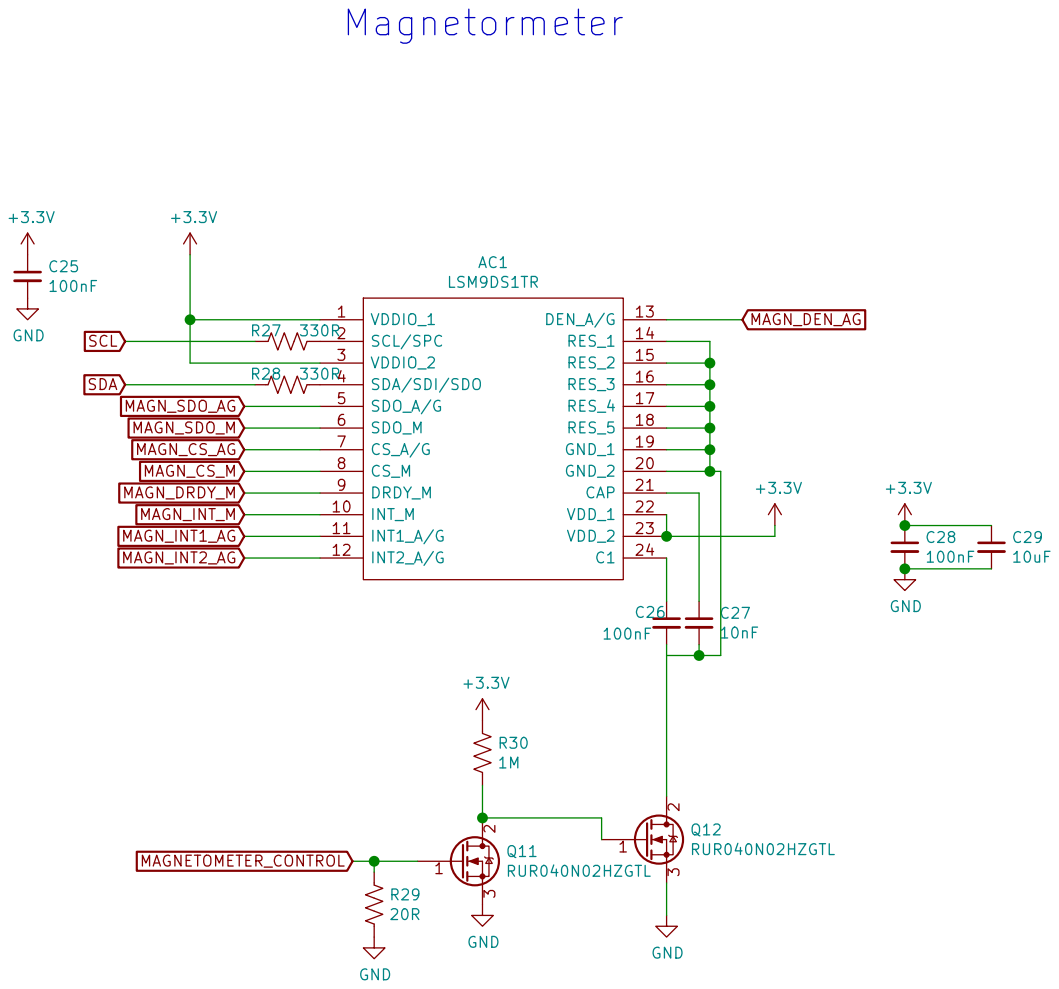
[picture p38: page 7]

Author: Romain Cocogne
Polytech Nice
Sheet: /magnetometer/
File: magnetometer.sch
Id: 7/11 Title: Prototype 2 Schematic

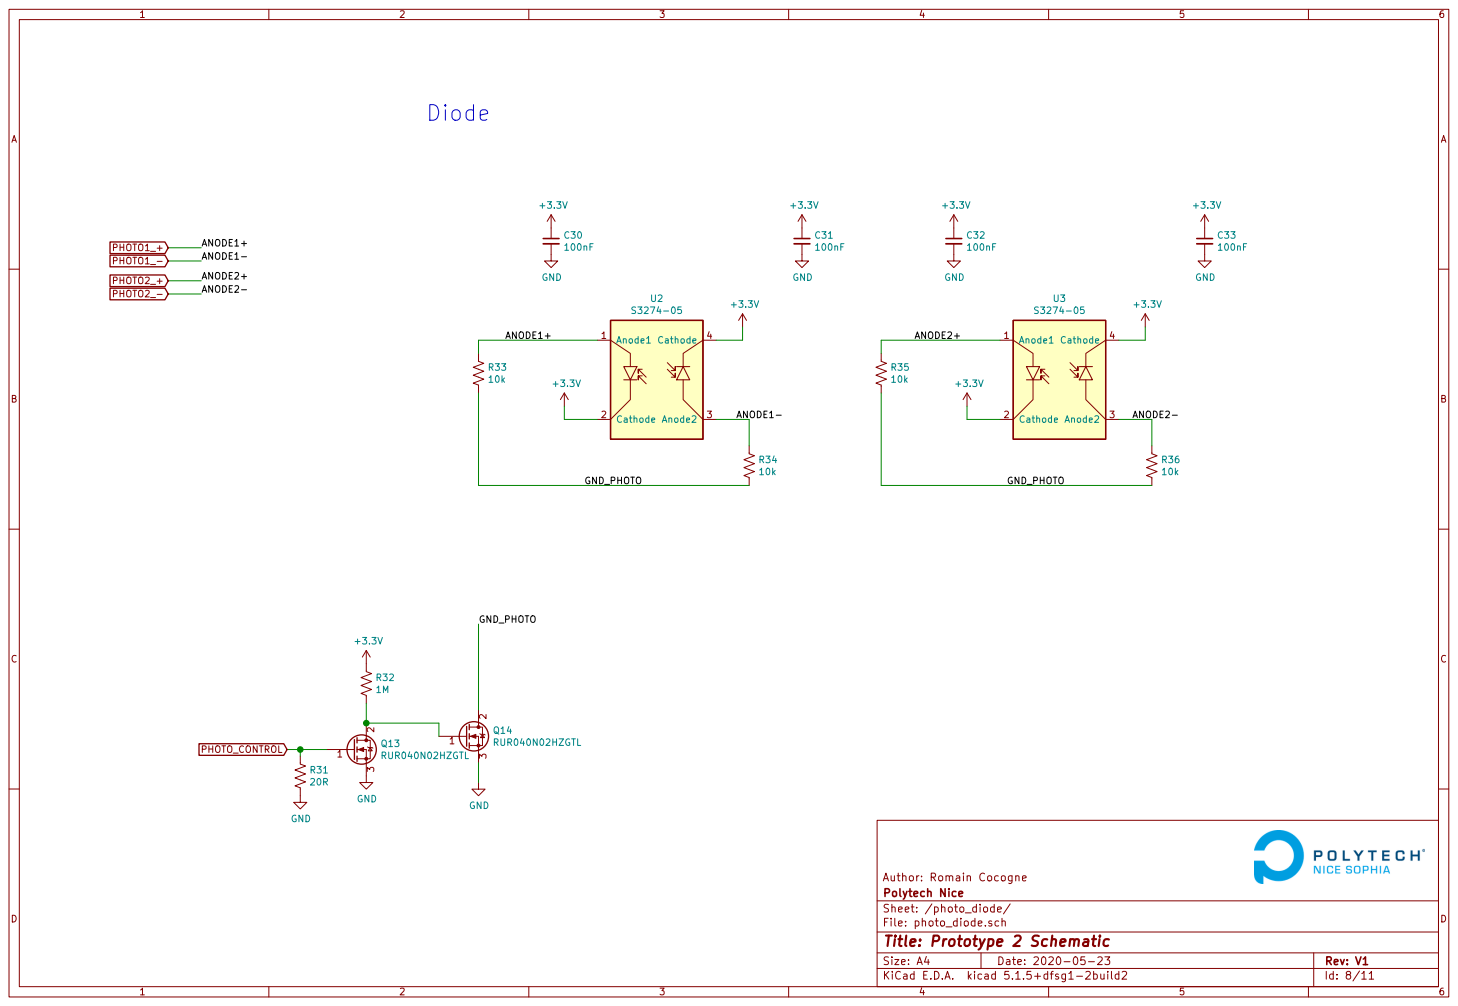
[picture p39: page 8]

Polytech Nice
Sheet: /photo_diode/
File: photo_diode.sch
Id: 8/11 Title: Prototype 2 Schematic

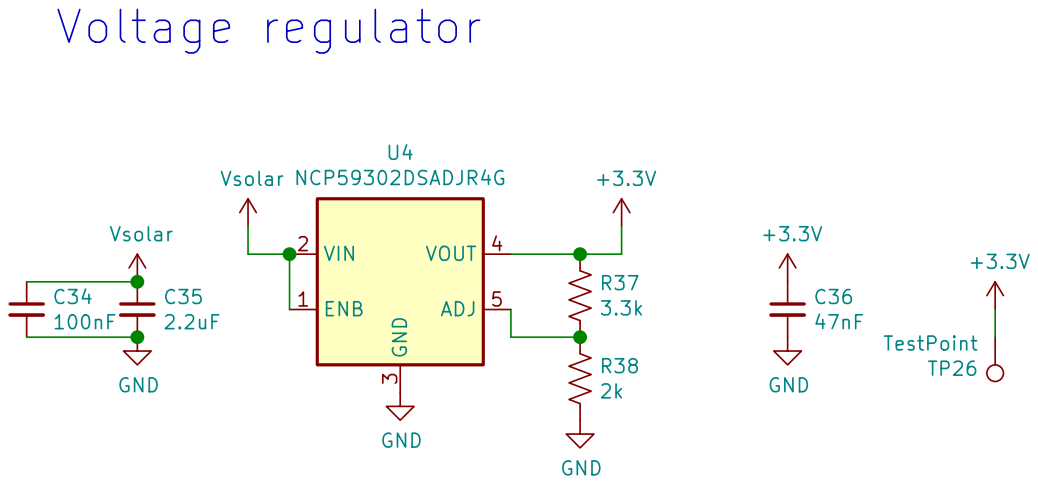
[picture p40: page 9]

Author: Romain Cocogne GND

Polytech Nice
Sheet: /regulateur_tension/
File: regulateur_tension.sch
Id: 9/11 Title: Prototype 2 Schematic

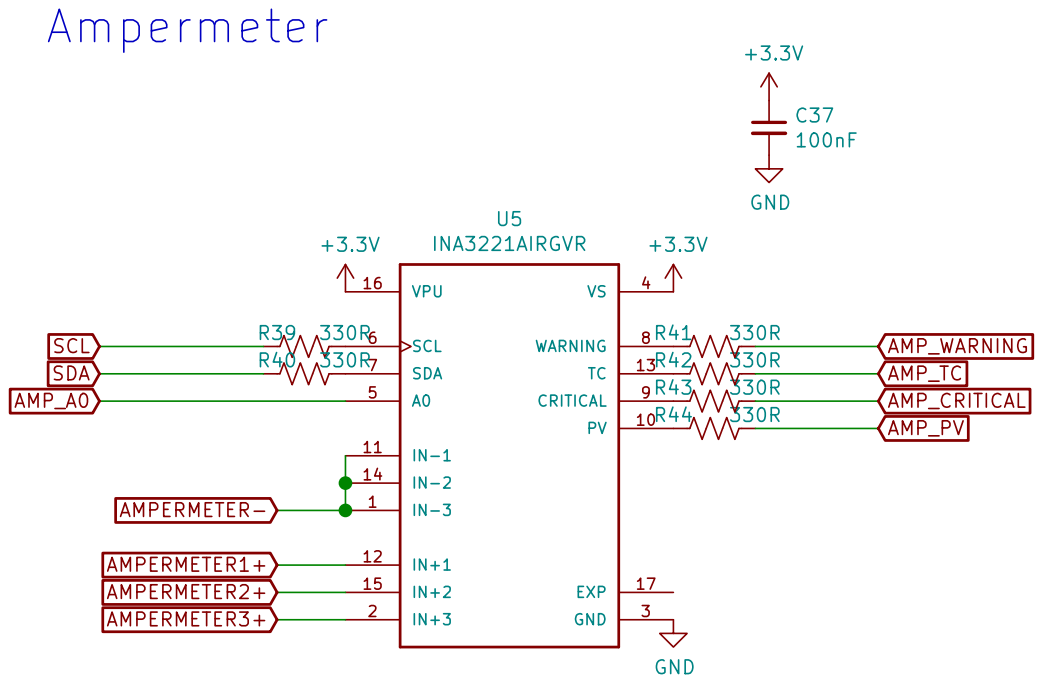
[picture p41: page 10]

Author: Romain Cocogne
Polytech Nice
Sheet: /ampermeter/
File: ampermeter.sch
Id: 10/11 Title: Prototype 2 Schematic

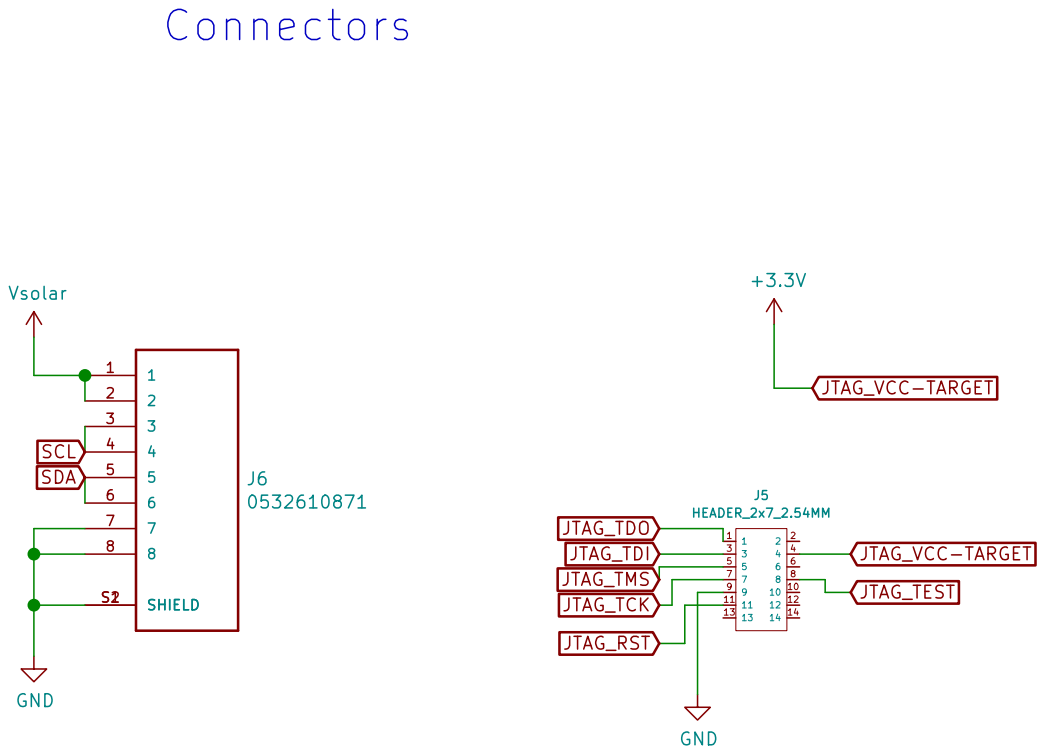
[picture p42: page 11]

Author: Romain Cocogne
File: connectors.sch Sheet: /connectors/ Polytech Nice

Id: 11/11 Title: Prototype 2 Schematic








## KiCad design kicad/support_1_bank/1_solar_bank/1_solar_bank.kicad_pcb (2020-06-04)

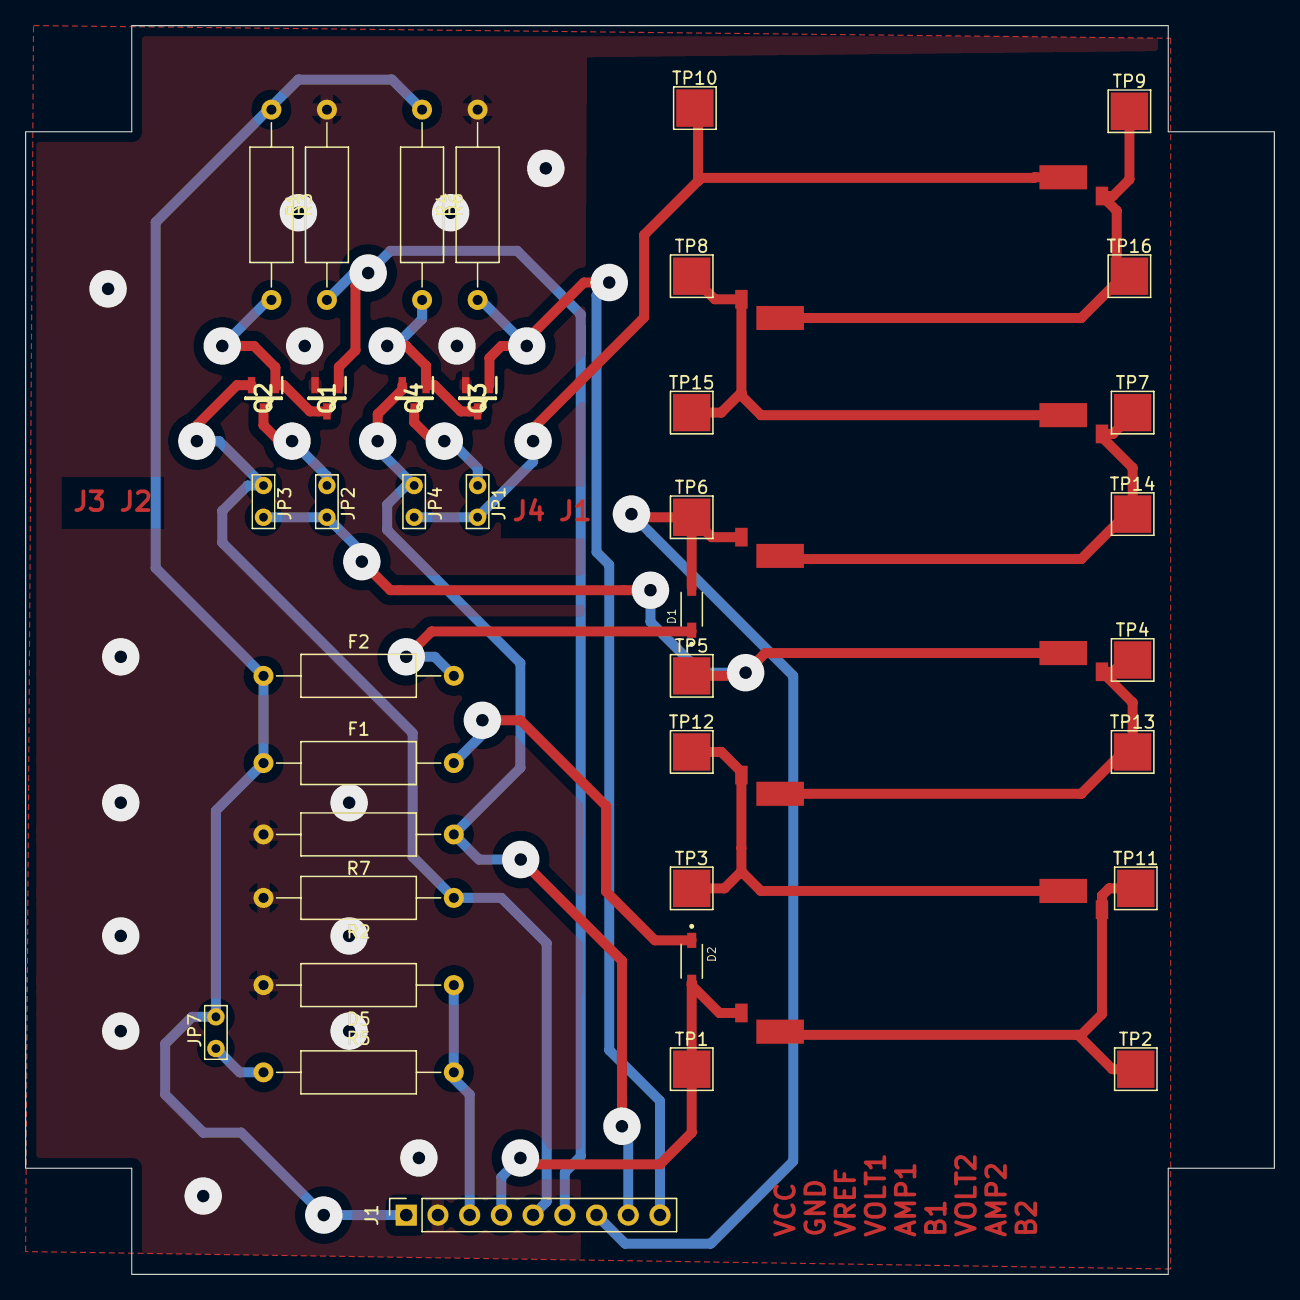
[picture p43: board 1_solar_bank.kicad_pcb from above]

Board: 2 copper layers, 100.0 x 100.0 mm, 46 parts (0 on the bottom side), 24 nets.

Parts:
D1, D2: D_Schottky; SOD3715X135N
D5: D_Zener; R_Axial_DIN0309_L9.0mm_D3.2mm_P15.24mm_Horizontal
F1, F2: Fuse_Small; R_Axial_DIN0309_L9.0mm_D3.2mm_P15.24mm_Horizontal
J1: Conn_01x09; PinSocket_1x09_P2.54mm_Vertical
JP1, JP2, JP3, JP4, JP7: Jumper_2_Bridged; TestPoint_Bridge_Pitch2.54mm_Drill0.7mm
Q1, Q2, Q3, Q4: RUR040N02HZGTL
R1, R2, R4, R7: 20R; R_Axial_DIN0309_L9.0mm_D3.2mm_P15.24mm_Horizontal
R3, R5, R6: 1M; R_Axial_DIN0309_L9.0mm_D3.2mm_P15.24mm_Horizontal
SC1, SC2, SC3, SC4, SC5, SC6, SC7, SC8: Solar_Cell; TRISOLX-T01
TP1, TP2, TP3, TP4, TP5, TP6, TP7, TP8, TP9, TP10, TP11, TP12, TP13, TP14, TP15, TP16: TestPoint; TestPoint_Pad_3.0x3.0mm

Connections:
+VSW: F1.1, F2.1, J1.1, JP7.1, R3.1, R6.1
AMPERMETER1: J1.5, JP3.2, Q2.3, R2.1
AMPERMETER2: J1.8, JP4.2, Q4.3, R7.1
BNK1_CONTROL: J1.6, Q1.1, R1.1
BNK2_CONTROL: J1.9, Q3.1, R4.1
GND: D5.2, J1.2, Q1.3, Q3.3, R1.2, R2.2, R4.2, R7.2
unnamed: D1.1, F2.2
unnamed: D2.1, F1.2
unnamed: JP1.1, JP4.1, SC8.2, TP10.1
unnamed: JP1.2, Q4.2
unnamed: JP2.1, JP3.1, SC4.2, TP5.1
unnamed: JP2.2, Q2.2
unnamed: JP7.2, R5.1
unnamed: Q1.2, Q2.1, R3.2
unnamed: Q3.2, Q4.1, R6.2
unnamed: SC1.2, SC2.1, TP2.1, TP11.1
unnamed: SC2.2, SC3.1, TP3.1, TP12.1
unnamed: SC3.2, SC4.1, TP4.1, TP13.1
unnamed: SC5.2, SC6.1, TP7.1, TP14.1
unnamed: SC6.2, SC7.1, TP8.1, TP15.1
unnamed: SC7.2, SC8.1, TP9.1, TP16.1
VOLTMETER1: D2.2, J1.4, SC1.1, TP1.1
VOLTMETER2: D1.2, J1.7, SC5.1, TP6.1
V_REF: D5.1, J1.3, R5.2

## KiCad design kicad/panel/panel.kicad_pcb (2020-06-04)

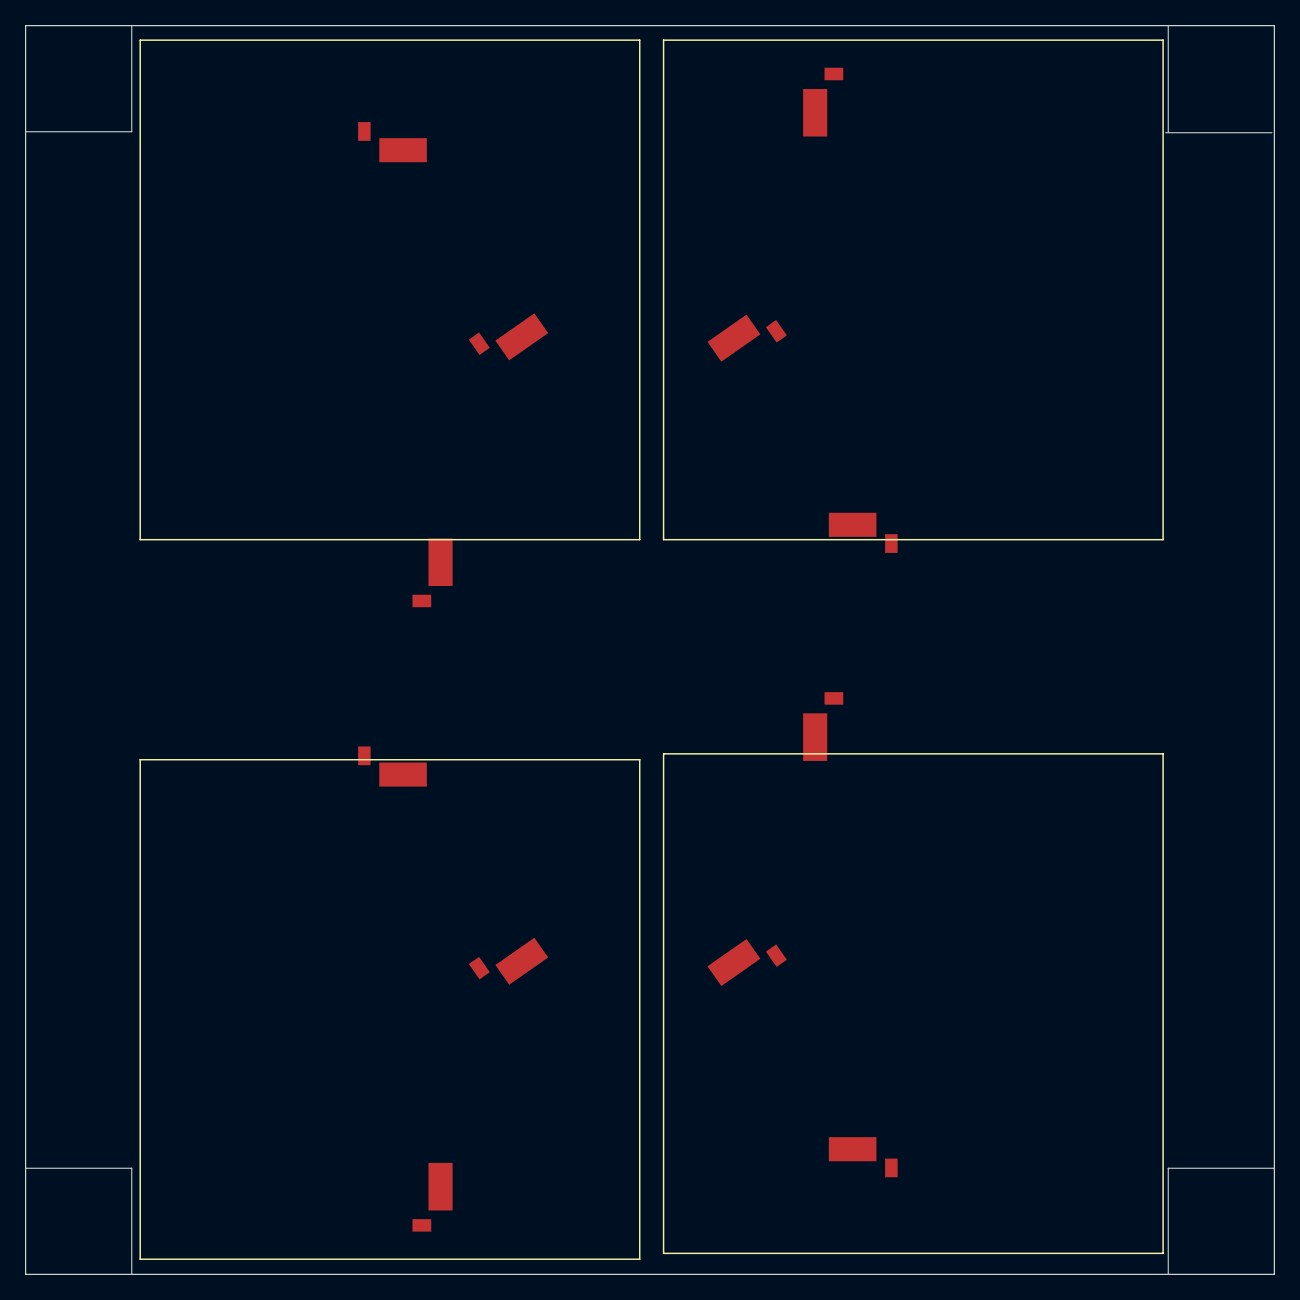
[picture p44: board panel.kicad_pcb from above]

Board: 2 copper layers, 100.0 x 100.0 mm, 12 parts (0 on the bottom side), 11 nets, no tracks yet.

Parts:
SC1, SC2, SC3, SC4, SC5, SC6, SC7, SC8, SC9, SC10, SC11, SC12: Solar_Cell; TRISOLX-T01

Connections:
GND: SC4.2, SC8.2, SC12.2
unnamed: SC1.2, SC2.1
unnamed: SC2.2, SC3.1
unnamed: SC3.2, SC4.1
unnamed: SC5.2, SC6.1
unnamed: SC6.2, SC7.1
unnamed: SC7.2, SC8.1
unnamed: SC9.2, SC10.1
unnamed: SC10.2, SC11.1
unnamed: SC11.2, SC12.1
VCC: SC1.1, SC5.1, SC9.1

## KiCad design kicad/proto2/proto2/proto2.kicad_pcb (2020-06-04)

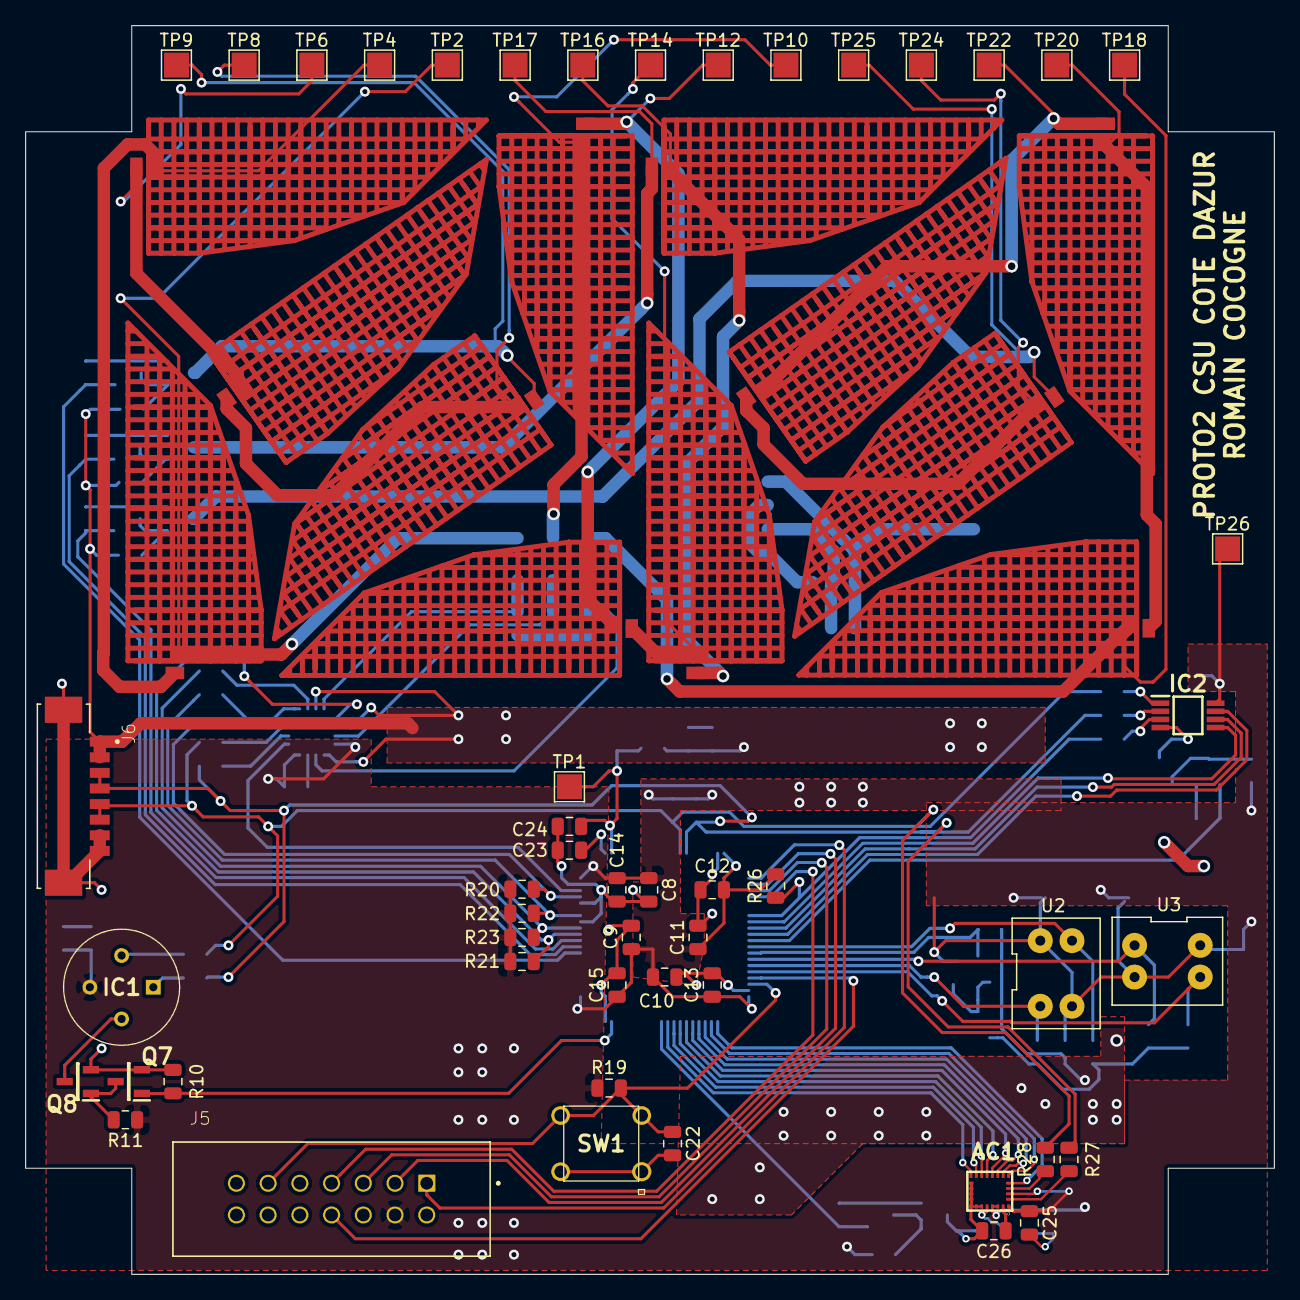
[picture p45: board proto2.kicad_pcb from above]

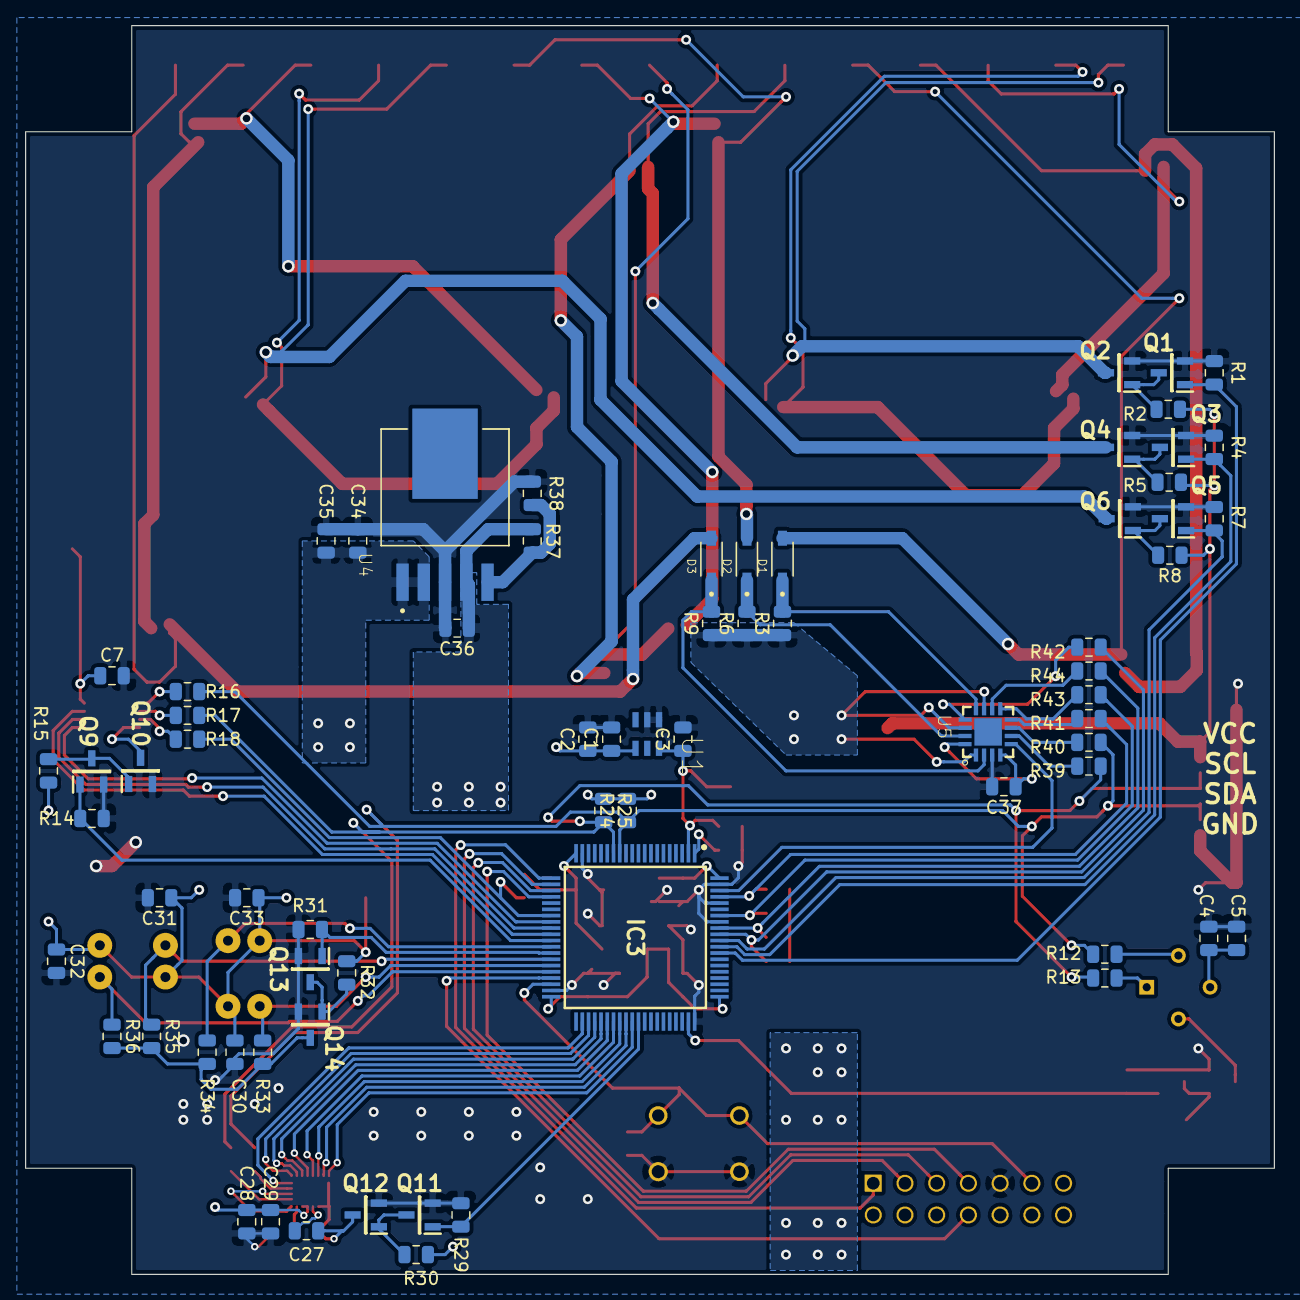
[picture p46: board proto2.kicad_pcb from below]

Board: 2 copper layers, 100.0 x 100.0 mm, 132 parts (70 on the bottom side), 87 nets.

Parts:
AC1: LSM9DS1TR; LGA-24L_3X3.5X1MM_
C1, C5, C7, C23, C24, C25, C26, C28, C30, C31, C32, C33, C34, C37: 100nF; C_0805_2012Metric
C2, C3: 1uF; C_0805_2012Metric
C4, C8, C9, C10, C11, C29: 10uF; C_0805_2012Metric
C12, C13, C14, C15, C27: 10nF; C_0805_2012Metric
C22: 2.2nF; C_0805_2012Metric
C35: 2.2uF; C_0805_2012Metric
C36: 47nF; C_0805_2012Metric
D1, D2, D3: D_Schottky; SOD3715X135N
IC1: MLX90641ESF-BAA-000-TU; MLX90621ESFBAB000SP
IC2: PCT2075DP,118; SOP65P490X110-8N
IC3: MSP430FR5964IPNR; QFP50P1400X1400X160-80N
J5: HEADER_2x7_2.54MM; TE_5104338-2
J6: 0532610871; MOLEX_0532610871
Q1, Q2, Q3, Q4, Q5, Q6, Q7, Q8, Q9, Q10, Q11, Q12, Q13, Q14: RUR040N02HZGTL
R1, R4, R7, R10, R14, R29, R31: 20R; R_0805_2012Metric
R2, R5, R8, R11, R15, R30, R32: 1M; R_0805_2012Metric
R3, R6, R9: 100mR; R_0805_2012Metric
R12, R13, R16, R17, R18, R27, R28, R39, R40, R41, R42, R43, R44: 330R; R_0805_2012Metric
R19: 47kR; R_0805_2012Metric
R20, R21, R22, R23, R24, R25, R26, R33, R34, R35, R36: 10k; R_0805_2012Metric
R37: 3.3k; R_0805_2012Metric
R38: 2k; R_0805_2012Metric
SC1, SC2, SC3, SC4, SC5, SC6, SC7, SC8, SC9, SC10, SC11, SC12: Solar_Cell; TRISOLX-T01
SW1: BP_DROIT_TRAV-switch; switch_fsm6jh_tyco
TP1, TP2, TP4, TP6, TP8, TP9, TP10, TP12, TP14, TP16, TP17, TP18, TP20, TP22, TP24, TP25, TP26: TestPoint; TestPoint_Pad_2.0x2.0mm
U1: LT1790ACS6-1.25TRMPBF; SOT95P280X100-6N
U2, U3: S3274-05
U4: NCP59302DSADJR4G
U5: INA3221AIRGVR; QFN65P400X400X100-17N

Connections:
/photo_diode/GND_PHOTO: Q14.2, R33.2, R34.2, R35.2, R36.2
AMPERMETER1+: D1.1, R3.2, U5.12
AMPERMETER2+: D2.1, R6.2, U5.15
AMPERMETER3+: D3.1, R9.2, U5.2
AMPERMETER-: C1.1, C2.1, C34.1, C35.1, J6.1, J6.2, R2.1, R3.1, R5.1, R6.1, R8.1, R9.1, U1.4, U4.1, U4.2, U5.1, U5.11, U5.14
AMP_A0: IC3.78, U5.5
AMP_CRITICAL: IC3.74, R22.1, R43.1
AMP_PV: IC3.72, R23.2, R44.1
AMP_TC: IC3.71, R21.2, R42.1
AMP_WARNING: IC3.77, R20.1, R41.1
BNK1_CONTROL: IC3.68, Q1.1, R1.1
BNK2_CONTROL: IC3.69, Q3.1, R4.1
BNK3_CONTROL: IC3.70, Q5.1, R7.1
CAMERA_CONTROL: IC3.59, Q7.1, R10.1
JTAG_RST: C22.1, IC3.38, J5.11, R19.2, SW1.3, SW1.4
JTAG_TCK: IC3.24, J5.7
JTAG_TDI: IC3.22, J5.3
JTAG_TDO: IC3.21, J5.1
JTAG_TEST: IC3.37, J5.8
JTAG_TMS: IC3.23, J5.5
JTAG_VCC-TARGET: AC1.1, AC1.3, AC1.22, AC1.23, C4.1, C5.1, C7.1, C8.1, C9.1, C10.1, C11.1, C12.1, C13.1, C14.1, C15.1, C25.1, C28.1, C29.1, C30.1, C31.1, C32.1, C33.1, C36.1, C37.1, IC1.3, IC2.8, IC3.20, IC3.40, IC3.61, IC3.80, J5.4, R11.1, R15.1, R19.1, R20.2, R21.1, R22.2, R23.1, R24.2, R25.1, R26.2, R30.1, R32.1, R37.1, TP26.1, U2.2, U2.4, U3.2, U3.4, U4.4, U5.4, U5.16
MAGNETOMETER_CONTROL: IC3.51, Q11.1, R29.1
MAGN_CS_AG: AC1.7, IC3.44
MAGN_CS_M: AC1.8, IC3.45
MAGN_DEN_AG: AC1.13, IC3.50
MAGN_DRDY_M: AC1.9, IC3.46
MAGN_INT1_AG: AC1.11, IC3.48
MAGN_INT2_AG: AC1.12, IC3.49
MAGN_INT_M: AC1.10, IC3.47
MAGN_SDO_AG: AC1.5, IC3.42
MAGN_SDO_M: AC1.6, IC3.43
unnamed: AC1.2, R27.1
unnamed: AC1.4, R28.1
unnamed: AC1.14, AC1.15, AC1.16, AC1.17, AC1.18, AC1.19, AC1.20, C26.2, C27.2, Q12.2
unnamed: AC1.21, C27.1
unnamed: AC1.24, C26.1
unnamed: IC1.1, R13.2
unnamed: IC1.2, R12.2
unnamed: IC1.4, Q8.2
unnamed: IC2.1, R16.1
unnamed: IC2.2, R17.1
unnamed: IC2.3, R18.1
unnamed: IC2.4, Q10.2
unnamed: Q1.2, Q2.1, R2.2
unnamed: Q2.2, SC4.2, TP9.1
unnamed: Q3.2, Q4.1, R5.2
unnamed: Q4.2, SC8.2, TP17.1
unnamed: Q5.2, Q6.1, R8.2
unnamed: Q6.2, SC12.2, TP25.1
unnamed: Q7.2, Q8.1, R11.2
unnamed: Q9.2, Q10.1, R15.2
unnamed: Q11.2, Q12.1, R30.2
unnamed: Q13.2, Q14.1, R32.2
unnamed: R37.2, R38.1, U4.5
unnamed: R39.1, U5.6
unnamed: R40.1, U5.7
unnamed: R41.2, U5.8
unnamed: R42.2, U5.13
unnamed: R43.2, U5.9
unnamed: R44.2, U5.10
unnamed: SC1.2, SC2.1, TP4.1
unnamed: SC2.2, SC3.1, TP6.1
unnamed: SC3.2, SC4.1, TP8.1
unnamed: SC5.2, SC6.1, TP12.1
unnamed: SC6.2, SC7.1, TP14.1
unnamed: SC7.2, SC8.1, TP16.1
unnamed: SC9.2, SC10.1, TP20.1
unnamed: SC10.2, SC11.1, TP22.1
unnamed: SC11.2, SC12.1, TP24.1
PHOTO1_+: IC3.35, R33.1, U2.1
PHOTO1_-: IC3.32, R34.1, U2.3
PHOTO2_+: IC3.34, R35.1, U3.1
PHOTO2_-: IC3.36, R36.1, U3.3
PHOTO_CONTROL: IC3.33, Q13.1, R31.1
SCL: IC3.14, J6.3, J6.4, R13.1, R17.2, R25.2, R27.2, R39.2
SDA: IC3.13, J6.5, J6.6, R12.1, R16.2, R24.1, R28.2, R40.2
TEMP-A0: IC2.7, IC3.30
TEMPERATURE_CONTROL: IC3.31, Q9.1, R14.1
TEMP_A1: IC2.6, IC3.29
TEMP_A2: IC2.5, IC3.28
TEMP_INT: IC3.27, R18.2, R26.1
UC1: C24.2, IC3.1
UC2: C3.1, C23.1, IC3.2, TP1.1, U1.6
UC19: C1.2, C2.2, C3.2, C4.2, C5.2, C7.2, C8.2, C9.2, C10.2, C11.2, C12.2, C13.2, C14.2, C15.2, C22.2, C23.2, C24.1, C25.2, C28.2, C29.2, C30.2, C31.2, C32.2, C33.2, C34.2, C35.2, C36.2, C37.2, IC3.19, IC3.39, IC3.60, IC3.73, IC3.76, IC3.79, J5.9, J6.7, J6.8, J6.S1, J6.S2, Q1.3, Q2.3, Q3.3, Q4.3, Q5.3, Q6.3, Q7.3, Q8.3, Q9.3, Q10.3, Q11.3, Q12.3, Q13.3, Q14.3, R1.2, R4.2, R7.2, R10.2, R14.2, R29.2, R31.2, R38.2, SW1.1, SW1.2, U1.1, U1.2, U4.3, U5.3
VOLTMETER1: D1.2, SC1.1, TP2.1
VOLTMETER2: D2.2, SC5.1, TP10.1
VOLTMETER3: D3.2, SC9.1, TP18.1

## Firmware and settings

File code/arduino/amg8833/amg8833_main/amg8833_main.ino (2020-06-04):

#include <MatrixMath.h>
#include <Wire.h>
#include <Adafruit_AMG88xx.h>
#include <math.h>


Adafruit_AMG88xx amg;

const uint8_t ROW_SIZE = 8;
const uint8_t COL_SIZE = 8;
const float THRESHOLD = 10;

float pixels[ROW_SIZE][COL_SIZE];
LinearRegression horizon(0, COL_SIZE);
mtx_type horizonMTX_x[ROW_SIZE];
mtx_type horizonMTX_y[COL_SIZE];

uint8_t rank_mat_x, rank_mat_y;

void setup() {
  Serial.begin(9600);
  Serial.println(F("\nAMG88xx pixels"));

  bool status;

  // default settings
  status = amg.begin();
  if (!status) {
    Serial.println("Could not find a valid AMG88xx sensor, check wiring!");
    while (!(status = amg.begin()));
  }

  Serial.println("-- Pixels Test --");

  Serial.println();

  delay(100); // let sensor boot up
}


void loop() {
  //read all the pixels
  amg.readPixels((float*)pixels);
  empty_coeff();

  find_horizon();
  //print_pixels();

  print_angles();

  //delay a second
  delay(500);
}

void find_horizon() {
  for (uint8_t x = 0; x < ROW_SIZE - 1; ++x) {
    for (uint8_t y = 0; y < COL_SIZE - 1; ++y) {
      if ((pixels[x + 1][y]) < 0 && (pixels[x][y]) > 0) {
        horizon.learn(x + 1, y);
        horizonMTX_x[x + 1] = -y;
        ++rank_mat_x;
      }
      if ((pixels[x][y + 1]) < 0 && pixels[x][y] > 0) {
        horizon.learn(x, y + 1);
        horizonMTX_y[y + 1] = -x;
        ++rank_mat_y;
      }
      if ((pixels[x + 1][y]) > 0 && (pixels[x][y]) < 0) {
        horizon.learn(x, y);
        horizonMTX_x[x] = y;
        ++rank_mat_x;
      }
      if ((pixels[x][y + 1]) > 0 && pixels[x][y] < 0) {
        horizon.learn(x, y);
        horizonMTX_y[y] = x;
        ++rank_mat_y;
      }
    }
  }
}

void empty_coeff () {
  horizon.reset();
  rank_mat_x = 0;
  rank_mat_y = 0;
}


void print_pixels () {
  Serial.print("[");
  for (uint8_t x = 0; x < ROW_SIZE; ++x) {
    for (uint8_t y = 0; y < COL_SIZE; ++y) {
      Serial.print(pixels[x][y]);
      Serial.print(", ");
    }
    Serial.println();
  }
  Serial.println("]");
  Serial.println();
}

void print_angles() {


  mtx_type coeffs_x[2] = {0, 0};
  mtx_type coeffs_y[2] = {0, 0};
  if ( rank_mat_x > 1) {
    LinearRegressionMTX linear_horizon (horizonMTX_x, rank_mat_x);
    linear_horizon.getCoeffs(coeffs_x);
  }
  if ( rank_mat_y > 1) {
    LinearRegressionMTX linear_horizon (horizonMTX_y, rank_mat_y);
    linear_horizon.getCoeffs(coeffs_y);
  }

  double alpha = 0;
  double beta = 0;

  if (coeffs_x[0] == 0) {
    alpha = PI / 2;
    beta = PI / 6 / 3.5 * (3.5 * (1 - coeffs_y[0]) - coeffs_y[1]) / (sqrt(coeffs_y[0] * coeffs_y[0] + 1));
  }
  else if (coeffs_y[0] == 0) {
    alpha = 0;
    beta = PI / 6 / 3.5 * (3.5 * (1 - coeffs_x[0]) - coeffs_x[1]) / (sqrt(coeffs_x[0] * coeffs_x[0] + 1));
  }
  else if (coeffs_x[0] != 0 && coeffs_y[0] != 0) {
    alpha = ((PI / 2 - atan2(11, coeffs_y[0])) * rank_mat_y + atan2(-1, coeffs_x[0]) * rank_mat_x) / (rank_mat_y + rank_mat_x);
    beta = PI / 6 / 3.5 * ((3.5 * (1 - coeffs_x[0]) - coeffs_x[1]) / (sqrt(coeffs_x[0] * coeffs_x[0] + 1)) * rank_mat_x
                           + (3.5 * (1 - coeffs_y[0]) - coeffs_y[1]) / (sqrt(coeffs_y[0] * coeffs_y[0] + 1)) * rank_mat_y)
           / (rank_mat_y + rank_mat_x);
  }

  Serial.println("{ ");
  Serial.print("\tangle alpha : "); Serial.println(alpha * 180 / PI);
  Serial.print("\thorizontal : "); Serial.println(beta * 180 / PI);
  Serial.println("}");
}

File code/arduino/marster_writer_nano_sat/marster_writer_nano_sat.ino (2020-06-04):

// Master writer for the NiceCube project
// by Quentin Combal

// Based on the Wire Master Writer example 
// by Nicholas Zambetti <http://www.zambetti.com>

// This program was made as a demo of the test_i2c_slave program
// running on an MSP430 microcontroller

// Demonstrates the communication protocol used between the MSP430
// microcontroller and the central unit of the nano satellite

// The arduno board acts as the central unit and is the master on 
// the i2c bus. It emmits commands to the slave to read values from
// different sensors attached to the slave, or to perform status checks

// The possible commands are :
//    -READ_SENSOR : ask for a sensor's value. Sensor is specified
//                   with a parameter (ex : PARAM_SENSOR1)
//    -LIST_SENSOR : ask for a list of avaiable sensors
//    -CONROLLER_STATUS: ask for a controller status check
//    -CELLS_StATUS: ask for a status check of the solar cells
   
// The micro controller acts as the slave. It receives commands from 
// the arduino and send back the desired data. Code for the slave can
// be found in the test_i2c_slave CCS project 

////////////////////////////////////////////////////////////////////////

#include <Wire.h>

#define SLAVE_ADDR          0x40
#define READ_SENSOR         0x01
#define LIST_SENSORS        0x02
#define CONTROLLER_STATUS   0x03
#define CELLS_STATUS        0x04

#define PARAM_SENSOR1       0x01
#define PARAM_SENSOR2       0x02
#define PARAM_SENSOR3       0x03
#define PARAM_ALL_SENSORS   0x04

void setup() {
  Serial.begin(9600);
  Serial.println("Begin setup");
  Wire.begin(); // join i2c bus (address optional for master)
  Serial.println("Setup done");
}

int16_t sensor1_data = 0;
int32_t sensor2_data = 0;
int8_t  sensor3_data = 0;

void loop() {
  Serial.println("Start communication");

  // Get sensor 2 data
  Wire.beginTransmission(SLAVE_ADDR); // transmit to slave device
  Wire.write(READ_SENSOR);              // sends command
  Wire.write(PARAM_SENSOR1);
  Wire.endTransmission();
  Wire.requestFrom(SLAVE_ADDR,2); // read the returned value
  while (Wire.available()){
    Serial.print("Data from sensor 1 : ");
    sensor1_data = Wire.read();
    sensor1_data |= Wire.read()<<8;
    Serial.println(sensor1_data*0.125);
  }
  
  // Get sensor 2 data
  Wire.beginTransmission(SLAVE_ADDR); // transmit to slave device
  Wire.write(READ_SENSOR);              // sends command
  Wire.write(PARAM_SENSOR2);
  Wire.endTransmission();
  Wire.requestFrom(SLAVE_ADDR,4); // read the returned value
  while (Wire.available()){
    Serial.print("Data from sensor 2 : ");
    sensor2_data = Wire.read();
    sensor2_data |= Wire.read()<<8;
    sensor2_data |= Wire.read()<<16;
    sensor2_data |= Wire.read()<<24;
    Serial.println(sensor2_data);
  }

  // Get sensor 3 data
  Wire.beginTransmission(SLAVE_ADDR); // transmit to slave device
  Wire.write(READ_SENSOR);              // sends command
  Wire.write(PARAM_SENSOR3);
  Wire.endTransmission();
  Wire.requestFrom(SLAVE_ADDR,1); // read the returned value
  while (Wire.available()){
    Serial.print("Data from sensor 3 : ");
    sensor3_data = Wire.read();
    Serial.println(sensor3_data);
  }

  // Get data from every sensor at once
  Wire.beginTransmission(SLAVE_ADDR); // transmit to slave device
  Wire.write(READ_SENSOR);              // sends command
  Wire.write(PARAM_ALL_SENSORS);
  Wire.endTransmission();
  Wire.requestFrom(SLAVE_ADDR,7); // read the returned value
  Serial.println("All sensors in one message : ");
  while (Wire.available()){
    Serial.print("  Sensor 1 : ");
    sensor1_data = Wire.read();
    sensor1_data |= Wire.read()<<8;
    Serial.println(sensor1_data*0.125);
    Serial.print("  Sensor 2 : ");
    sensor2_data = Wire.read();
    sensor2_data |= Wire.read()<<8;
    sensor2_data |= Wire.read()<<16;
    sensor2_data |= Wire.read()<<24;
    Serial.println(sensor2_data);
    Serial.print("  Sensor 3 : ");
    sensor3_data = Wire.read();
    Serial.println(sensor3_data);
  }
  
  // Get sensors list
  Wire.beginTransmission(SLAVE_ADDR); // transmit to slave device
  Wire.write(LIST_SENSORS);              // sends command
  Wire.endTransmission();
  Serial.println("List of sensors :");
  // 96 characters to be received
  // The Wire library buffer has a size of 32 bytes 
  // Read the returned value in packets of 32 bits
  for (int i=0; i<3; i++){  
    Wire.requestFrom(SLAVE_ADDR,32); 
    while (Wire.available()){
      Serial.print((char)Wire.read());
    }
  }

  // Get controller status
  Wire.beginTransmission(SLAVE_ADDR); // transmit to slave device
  Wire.write(CONTROLLER_STATUS);              // sends command
  Wire.endTransmission();
  Wire.requestFrom(SLAVE_ADDR,32); // read the returned value
  Serial.print("Controller status : ");
  while (Wire.available()){
    Serial.print((char)Wire.read());
  }
  Serial.println();

  // Get cells status
  Wire.beginTransmission(SLAVE_ADDR); // transmit to slave device
  Wire.write(CELLS_STATUS);              // sends command
  Wire.endTransmission();
  Wire.requestFrom(SLAVE_ADDR,32); // read the returned value
  Serial.print("Cells status : ");
  while (Wire.available()){
    Serial.print((char)Wire.read());
  }
  Serial.println();


  
  Serial.println("Done receiving");
  delay(5000);
}

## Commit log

2019-10-17 Add budget
    [budget projet tuto.xlsx]
2019-11-07 update gantt
    rajout de 3 tâches
2019-11-08 Ajout memo seance 3 et choix uControleur
    [uControleur.xlsx]
2019-11-15 datasheet diode zener 1.8
2019-11-15 Update BOM and GANTT
2019-11-28 cahier des charges
2020-02-07 add kicad
    [panel.kicad_pcb, panel.sch]
2020-02-07 mono cellule kicad schemas
    [1_solar_bank.kicad_pcb, 1_solar_bank.sch, panel.kicad_pcb]
2020-02-12 update panel schematic
    [1_solar_bank.kicad_pcb, 1_solar_bank.sch]
2020-02-13 proto1 panel
    [1_solar_bank.kicad_pcb]
2020-02-14 revision schemas + pcb
    [1_solar_bank-B_Cu.gbr, 1_solar_bank-B_Mask.gbr, 1_solar_bank-B_Paste.gbr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]
2020-02-21 Added CCS and Energia code for the MSP430 + datasheets
    [MCU021_V1.0.PrjPcb, MCU021_V1.0_CoverSheet.SchDoc, MCU021_V1.0_Hardware.SchDoc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]
2020-02-21 Added I2C_ping and Magnetometer programs for the MSP430
2020-03-06 Added functional code for the LSM9DS1 magnetometer
2020-03-19 update avec le code du capteur d'horizon
    [1_solar_bank.kicad_pcb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]
2020-03-20 Ajout du calcul de l'offset pour le capteur de temperature
2020-03-27 update 27/03/2020
    [camera.sch, proto2.kicad_pcb, proto2.sch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]
2020-04-08 Added CCS code for I2C connection and example code for TempSensor
    [MCU021_V1.0.PrjPcb, MCU021_V1.0_CoverSheet.SchDoc, MCU021_V1.0_Hardware.SchDoc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]
2020-04-24 update on proto2
    [ampermeter.sch, camera.sch, connectors.sch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]
2020-05-01 Added i2c slave code
    Added CCS code for the MSP430 to act as i2c slave with a arduino as a master
2020-05-02 V2 of test_i2c_slave program
    Updated the test_i2c_slave program to read different sensors. Also updated the master_receive arduino code
2020-05-15 Added mag sensor i2c communicaton example
2020-05-21 More commands for the i2c communication
    Added more commands to the i2c_slave program for the MSP430. Updated the master_writer arduino program to test those commands.
2020-05-23 pdf et png proto2
    [ampermeter.sch, camera.sch, connectors.sch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]
2020-05-23 BOM proto2 in exel
    [proto2_BOM.xlsx]
2020-05-23 BOM proto2
2020-05-23 proto1 schematic
    [1_solar_bank.sch, proto2.kicad_pcb]
2020-06-04 last commit romain windows
    [1_solar_bank-B_Cu.gbr, 1_solar_bank-B_Mask.gbr, 1_solar_bank-B_Paste.gbr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]
2020-06-04 Clean up
    Cleaned up the repository for future groups
    [MCU021_V1.0.PrjPcb, MCU021_V1.0_CoverSheet.SchDoc, MCU021_V1.0_Hardware.SchDoc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]
2020-06-04 Clean up 2
    [MCU021_V1.0.PrjPcb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]
2020-06-04 change proto2 kicad path so that it can be used in other PC
